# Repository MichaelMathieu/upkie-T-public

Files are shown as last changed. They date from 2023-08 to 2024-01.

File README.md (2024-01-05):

# Bill of materials

Quantity | Material | Link | Price (Unit)
--- | --- | --- | ---
TODO | PLA filament (or any non-flex filament) | |
TODO | Flex filament | |
7 | CAN bus cables (see below for lengths, JST-PH3 connectors) | |
7 | power cables (see below for lengths) | |
1 | Battery (12V to 44V, >= 2000mAh) with XT90 connector. Note: LiFe batteries are safer. | | 
1 | Battery charger | |
6 | QDD 100 beta 3 (NOT beta 2) | https://mjbots.com/products/qdd100-beta-3 | $539+VAT
2 | moteus dev kits | https://mjbots.com/products/moteus-r4-11-developer-kit | $244+VAT
1 | power dist board | https://mjbots.com/products/mjbots-power-dist-r4-5b | $149+VAT
1 | pi3hat | https://mjbots.com/products/mjbots-pi3hat-r4-5 | $149+VAT
1 | Raspberri by rev 4 | | £40 to £80 depending on RAM
1 | screen for raspberri pi (TODO) | https://www.amazon.co.uk/dp/B0B455LDKH?psc=1&ref=ppx_yo2ov_dt_b_product_details | £38
1 | ~30cm ribbon cable for the screen | https://www.amazon.co.uk/dp/B075PBTQPG?ref=ppx_yo2ov_dt_b_product_details&th=1 | £3
1 | slim 80x80 computer fan, 2 pins | https://amzn.eu/d/8T4fS8s | £10
6 | 608 bearings | | <£10
TODO | M3x6 socket head machine screws | |
TODO | M3x10 socket head machine screws | |
TODO | M3x20 socket head machine screws | |
TODO | M3 heat inserts | https://amzn.eu/d/d2RtyQ6 | £7
4 | M2.5 female to female 12mm (TODO confirm) spacers | https://www.amazon.co.uk/dp/B093FQH5WS?ref=ppx_yo2ov_dt_b_product_details&th=1 | <£10
4 | M2.5x8 | maybe above link |
1 | (Optional) bluetooth keyboard and mouse | | ~£25

# Cables

Try to get the lengths right. Slack can be annoying.

* For each tibia, one CAN and one power cable. Length: 290mm.
* For each femur, one CAN and one power cable. Length: 340mm.
* Power dist board -> left qdd: one power cable. Length: TODO.
* Power dist board -> right qdd: one power cable. Length: TODO.
* pi3hat -> left qdd: one CAN cable. Length: TODO.
* pi3hat -> right qdd: one CAN cable. Length: TODO.
* power dist board -> pi3hat: one power cable and one (optional) CAN cable. Length: TODO.
* Solder a xt30 connector to the fan to connect to the power dist board.

# 3d Print

Print all the `.stl` files. Some files have (or will have) a `.3mf` version if the print is difficult. Notes:
* The femurs and tibia print vertically. Adding a brim is recommended.
* Print the files with names starting with FLEX in flex filament.
* The tyres need to be softer than what you would get with the regular slicer settings. See the `.3mf` file, or experiment with slicer settings.
* The parts are designed to be printed with a maximum overhang threshold of 60 degrees. Anything lower may result in unwanted support (may be hard to remove).
* Files with x2 in the name need to be printed twice.
* There are several versions of the battery holder depending on the battery dimension.

# Assembly (unfinished)
Order of operation (experimental):
Legs (x2):
* Tyre on wheelset
* Screw wheelset to motor with 3 M3x10 screws (TODO confirm length)
* bearing in wheelset
* Insert motor plate into tibia
* Attach motor with 4 M3x20 screws (TODO)
* Add and attach ankle cap with 1 M3x6 or M3x10 screw
* Attach bottom ankle cap with 2 M3x10 screws (TODO)
* ...

# Notes
Wheel radius: 80.66mm

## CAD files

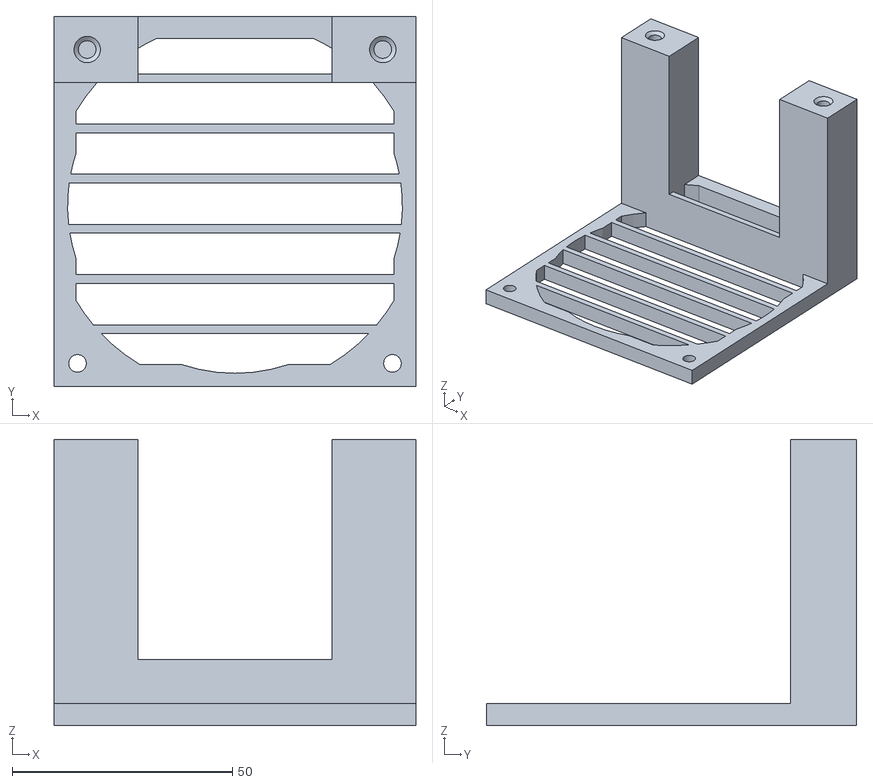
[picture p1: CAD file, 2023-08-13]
stl/battery holders/battery holder large.STL
82.1 x 84.0 x 65.0

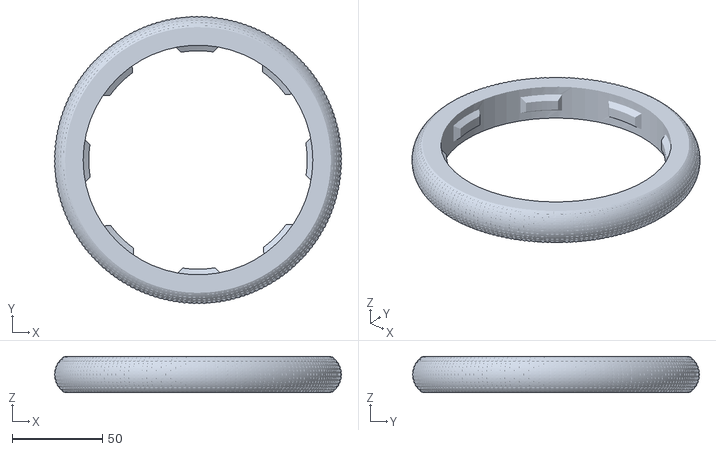
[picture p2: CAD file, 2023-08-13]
stl/FLEX tyre x2.STL
159.1 x 159.1 x 20.0

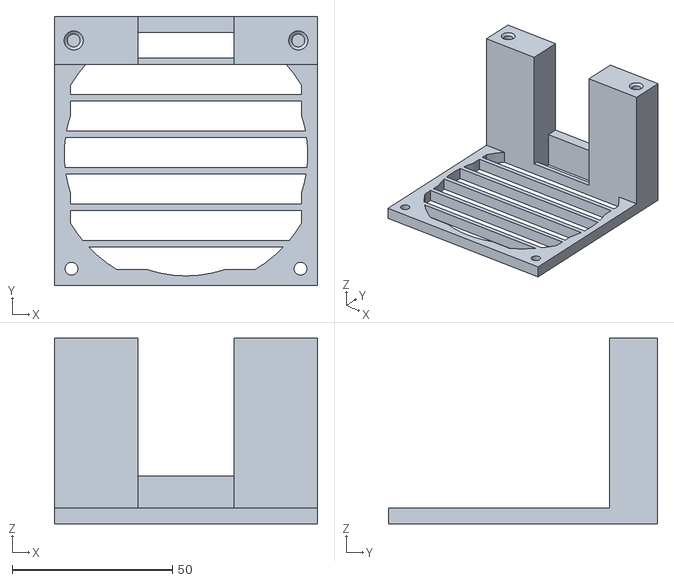
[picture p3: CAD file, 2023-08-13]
stl/battery holders/battery holder small.STL
82.1 x 84.0 x 58.0

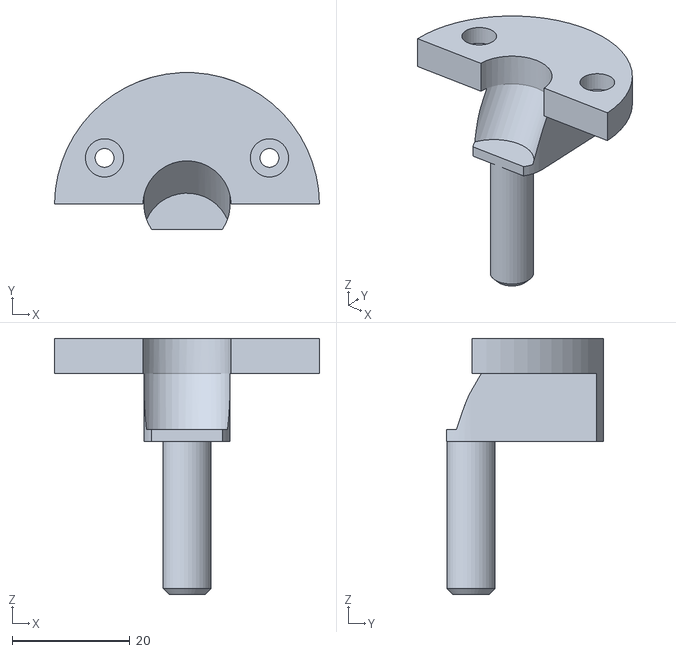
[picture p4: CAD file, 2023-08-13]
stl/hip cap x2.STL
45.0 x 26.6 x 43.5

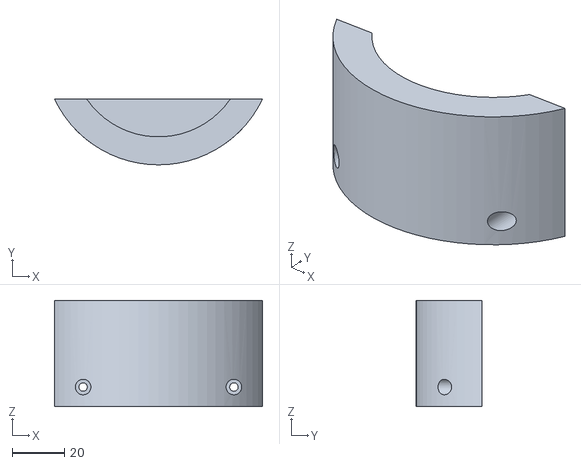
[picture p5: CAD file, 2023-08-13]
stl/ankle bottom x2.STL
80.0 x 25.3 x 40.8

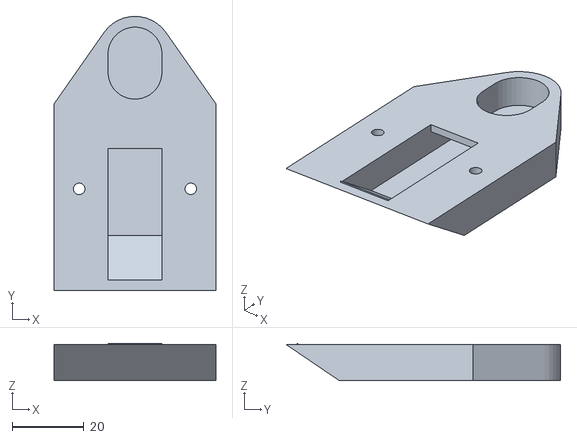
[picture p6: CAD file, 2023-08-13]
stl/knee wire cap x2.STL
45.0 x 76.2 x 10.4

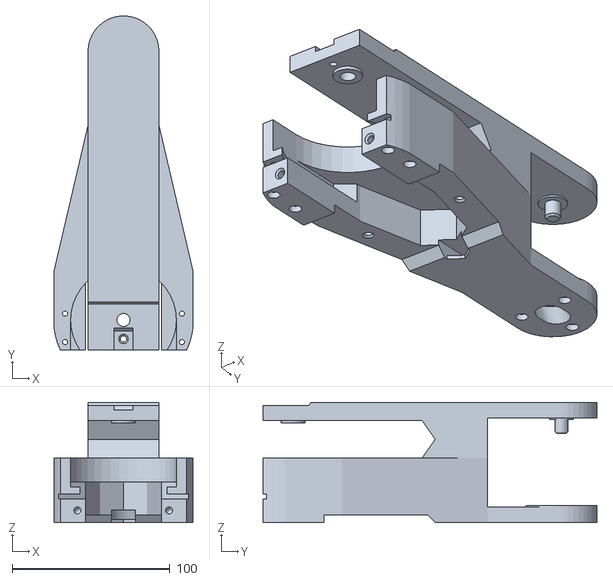
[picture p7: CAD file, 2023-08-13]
stl/tibia x2.STL
88.0 x 211.4 x 76.2

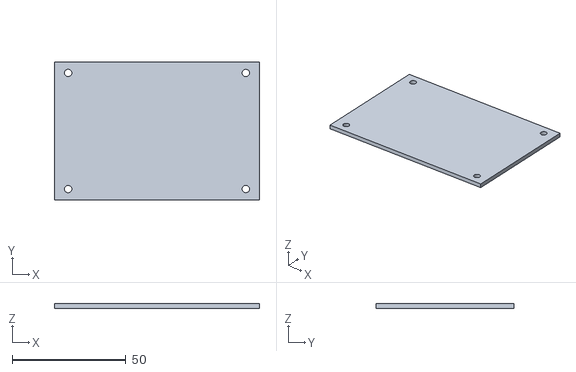
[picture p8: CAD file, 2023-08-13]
stl/body_wire_cap.STL
90.0 x 60.6 x 2.00

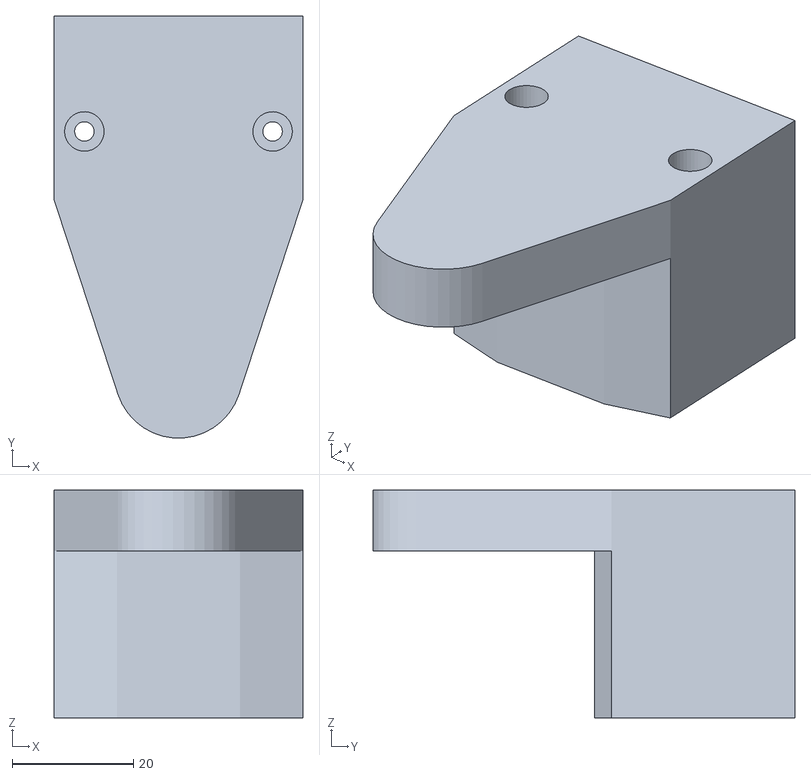
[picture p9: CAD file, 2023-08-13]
stl/hip wire cap x2.STL
41.0 x 69.5 x 37.5

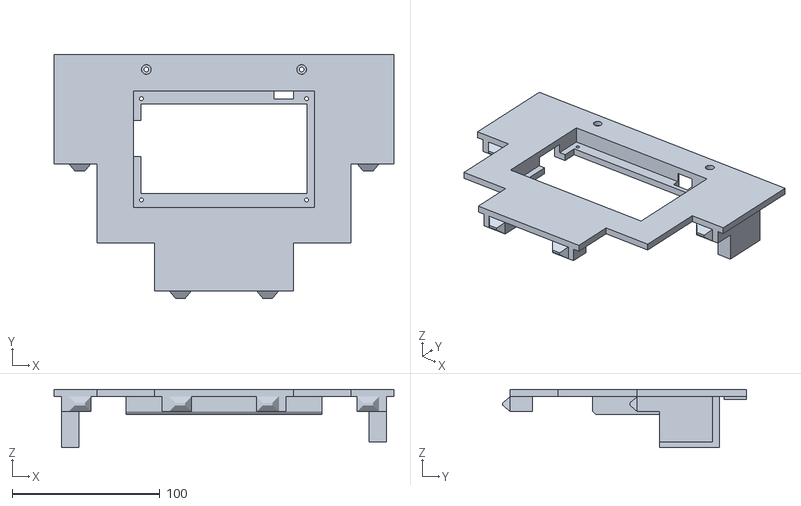
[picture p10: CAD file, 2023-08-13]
stl/front_plate.STL
230.0 x 164.8 x 39.5

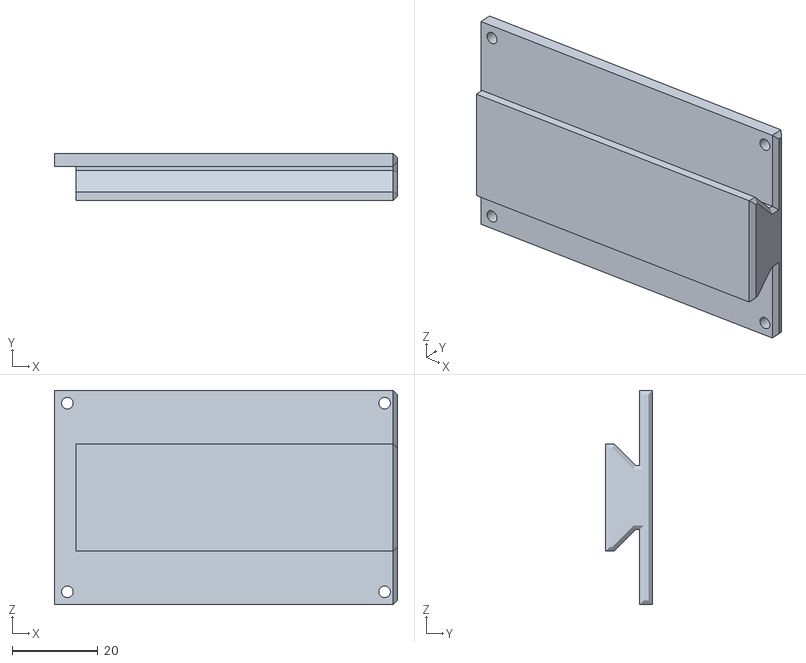
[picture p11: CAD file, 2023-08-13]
stl/powerboard holder.STL
80.0 x 11.0 x 50.0

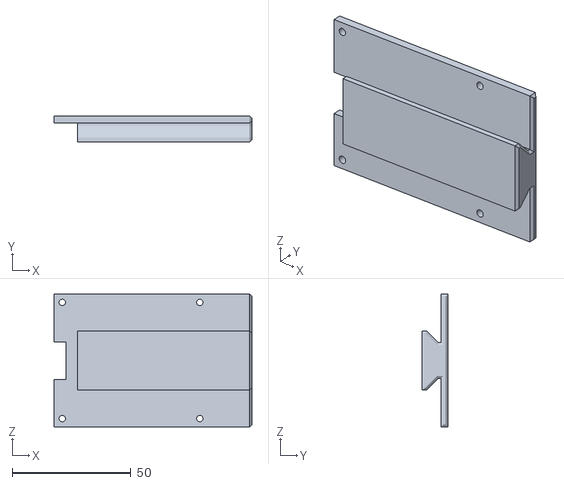
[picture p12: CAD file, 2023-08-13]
stl/raspi support.STL
83.5 x 11.0 x 56.0

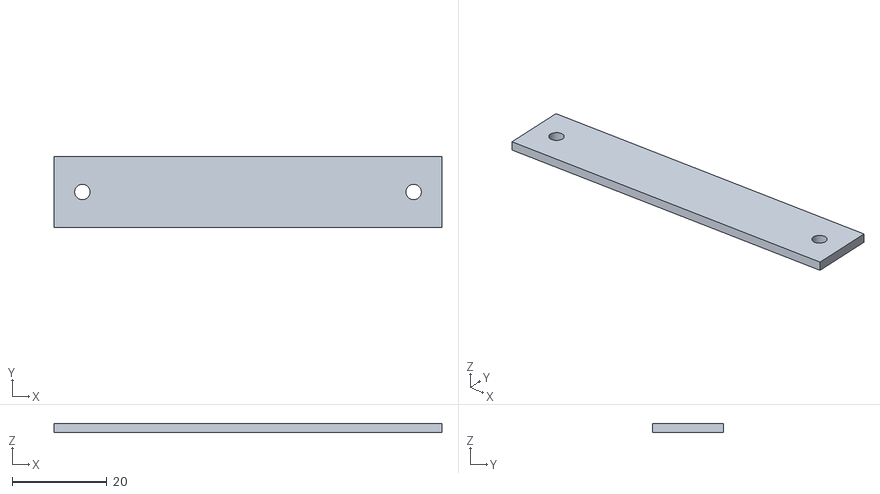
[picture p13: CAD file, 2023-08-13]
stl/FLEX battery strap.STL
82.1 x 15.0 x 2.00

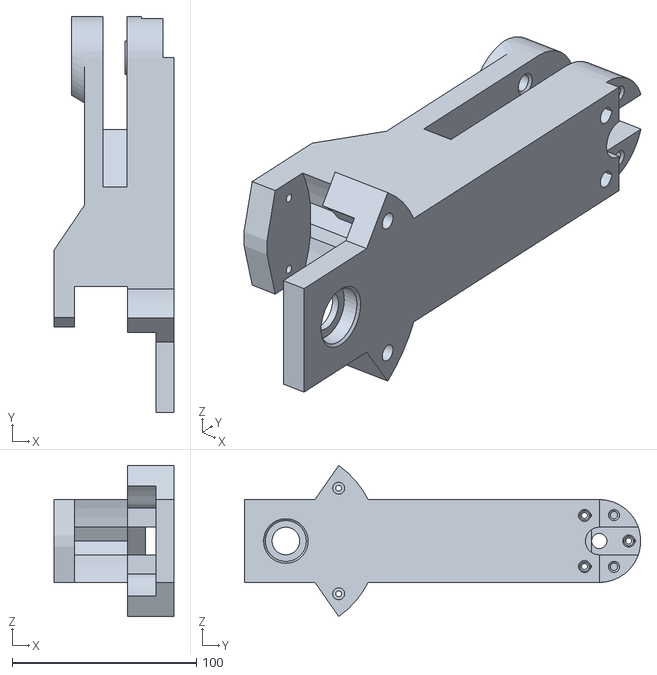
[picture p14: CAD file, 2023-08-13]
stl/femur x2.STL
65.0 x 214.9 x 81.9

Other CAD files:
stl/ankle x2.STL
stl/body.STL
stl/tibia upper cap x2.STL
stl/wheelset x2.STL
